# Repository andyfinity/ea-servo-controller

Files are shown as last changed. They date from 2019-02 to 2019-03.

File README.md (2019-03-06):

# ExperimentalAvionics Servo Controller

A simple circuit board with just enough smarts to move a servo motor between two adjustable locations.

## About

This project evolved from the need to replace a mechanical actuator inside the engine cowling of a small, experimental airplane.

Position input can be given by a switch, a potentiometer, or an analog signal. Power input is anything from 6V to 18V. Since a switching regulator is used, a higher voltage implies lower current. Servo output is 5V at up to 2A, where the position signal is a 0.5ms to 2.5ms pulse every 20ms.

For your convenience, pinouts are displayed on the back of the PCB.

[Online BOM with vendor links.](https://octopart.com/bom-tool/hhvvhDB6)

## Contributing

[Atmel Studio 7](https://www.microchip.com/mplab/avr-support/atmel-studio-7) is used to compile the source code. [pyupdi](https://github.com/mraardvark/pyupdi/) is then used to push the .hex file to the ATtiny402.

The serial port can be any 3.3V UART-to-USB device, but we used [this one](https://www.tinyosshop.com/index.php?route=product/product&product_id=600). 5V will probably work, but it's untested.

PRs are welcome. There's not a lot of hand-written source code, so just make your edits look nice. If you make any changes to the PCB or schematic, make sure ERC and DRC come back mostly clean.

## License

Everything is released under the GPLv3.

## TODO

* Release the source code and .hex file
* Show pictures in README
* Design basic enclosure
* Release PCB STEP file
* Think about replacing the ATtiny with a bunch of discrete parts
* Think about increasing the 5V rail to 6V to increase motor speed

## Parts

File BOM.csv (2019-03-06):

Qty | Manufacturer | MPN | Schematic Reference | Digi-Key SKU
1 | Microchip | ATTINY402-SSFR | U1 | ATTINY402-SSFRCT-ND
1 | Texas Instruments | TPS82140SILR | U2 | 296-48215-1-ND
2 | Microchip | MCP1754ST-3302E/CB | U3, U4 | MCP1754ST-3302E/CBCT-ND
1 | ON Semiconductor | BSS138 | Q1 | BSS138CT-ND
1 | Infineon | IRLML9301TRPBF | Q2 | IRLML9301TRPBFCT-ND
2 | Dialight | 598-8220-107F | D1, D2 | 350-2048-1-ND
1 | ON Semiconductor | SZMMSZ4697T1G | D3 | SZMMSZ4697T1GOSCT-ND
1 | Samsung | CL10B104KB8NNNC | C1 | 1276-1000-1-ND
2 | Samsung | CL21A475KAQNNNE | C2, C4 | 1276-1244-1-ND
2 | Samsung | CL21B105KAFNNNE | C3, C5 | 1276-1066-1-ND
2 | Samsung | CL31A106KAHNNNE | C6, C9 | 1276-1075-1-ND
1 | Murata | GRM219R61C226ME15L | C7 | 490-9952-1-ND
1 | Samsung | CL10B103KB8NCNC | C8 | 1276-1921-1-ND
2 | BI Technologies | 23BR500LFTR | R1, R2 | 987-1805-1-ND
1 | Panasonic | ERJ-3GEYJ472V | R5 | P4.7KGCT-ND
3 | Panasonic | ERJ-3GEYJ102V | R6, R7, R15 | P1.0KGCT-ND
5 | Panasonic | ERJ-3GEYJ101V | R4, R8, R9, R10, R13 | P100GCT-ND
2 | Panasonic | ERJ-3GEY0R00V | R3, R16 | P0.0GCT-ND
1 | Panasonic | ERJ-3EKF5233V | R11 | P523KHCT-ND
1 | Panasonic | ERJ-3EKF1003V | R12 | P100KHCT-ND
1 | FCI | LD09P24A4GV00LF | P1 | 609-5184-ND
1 | ON Semiconductor | MBR130LSFT1G | D4 | MBR130LSFT1GOSCT-ND

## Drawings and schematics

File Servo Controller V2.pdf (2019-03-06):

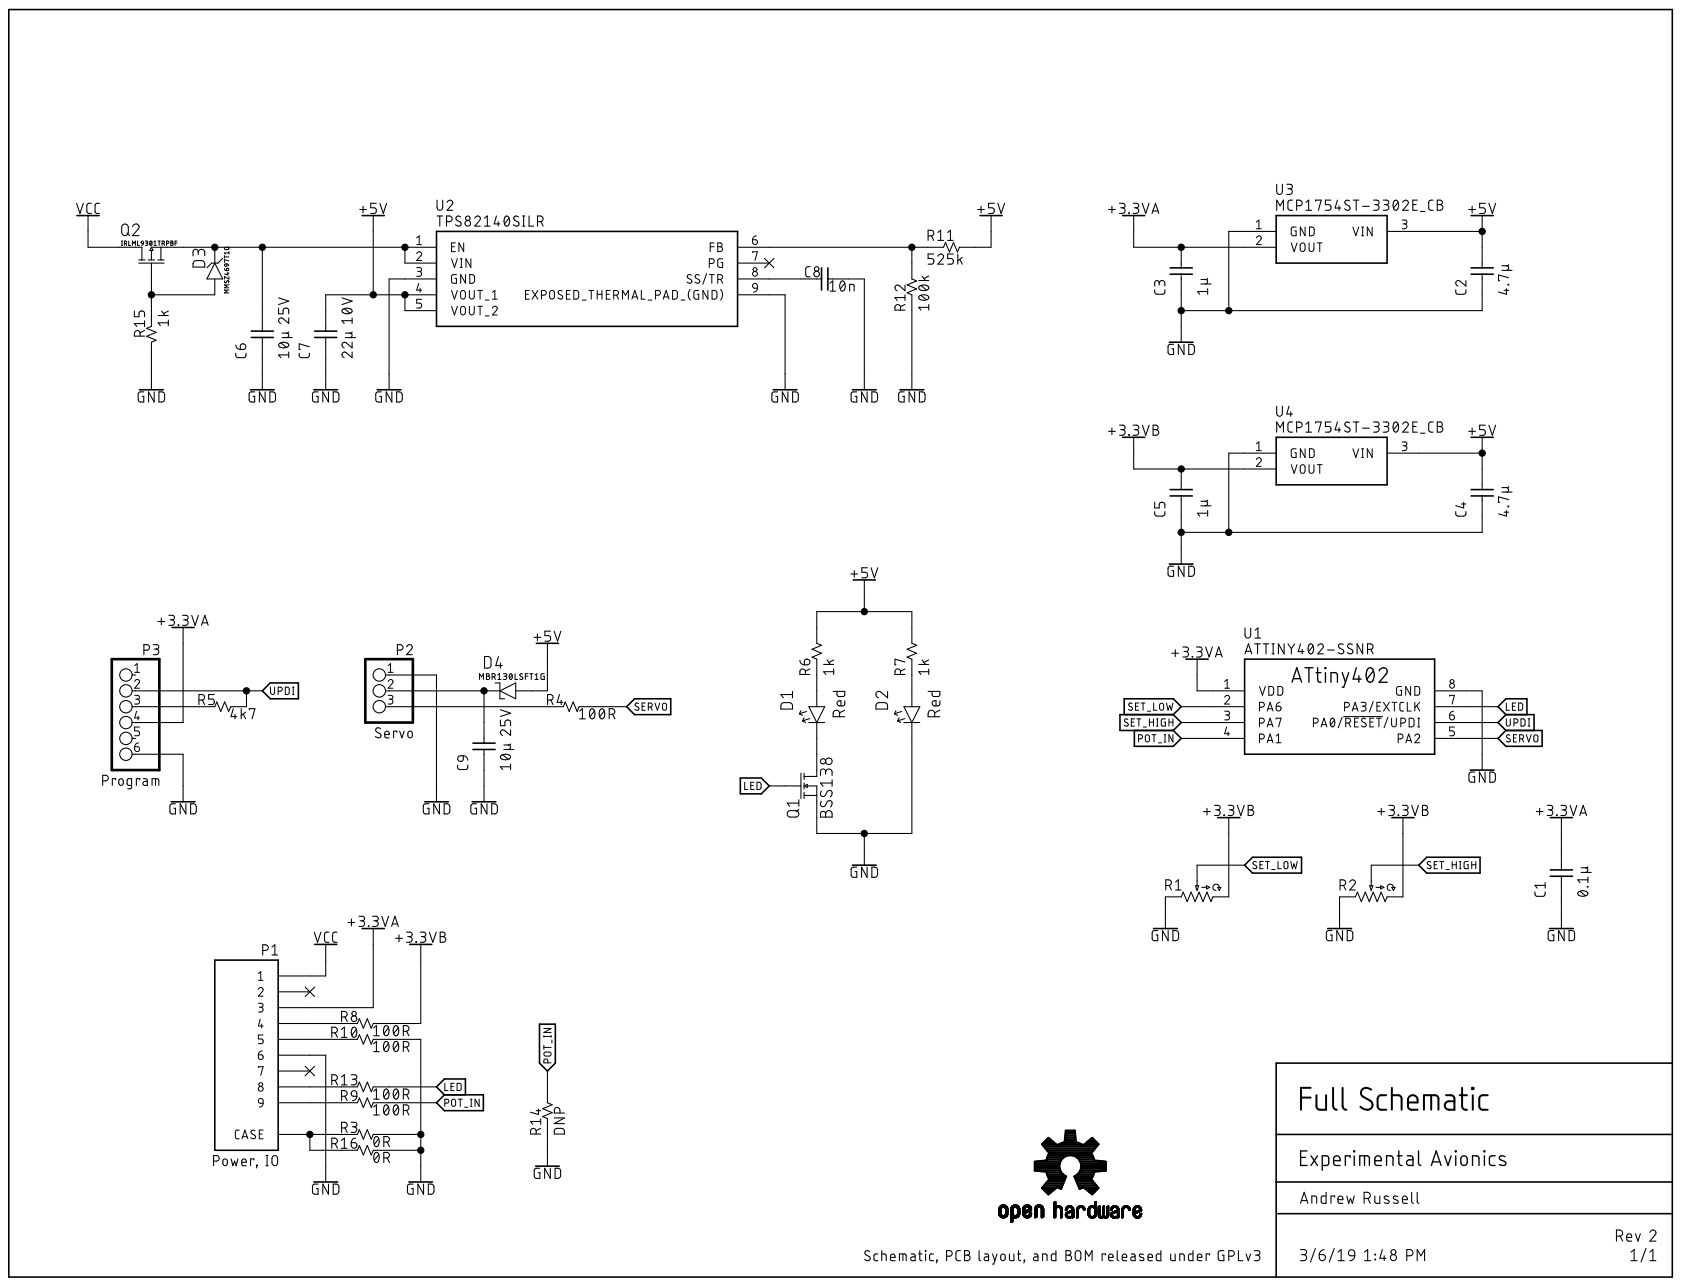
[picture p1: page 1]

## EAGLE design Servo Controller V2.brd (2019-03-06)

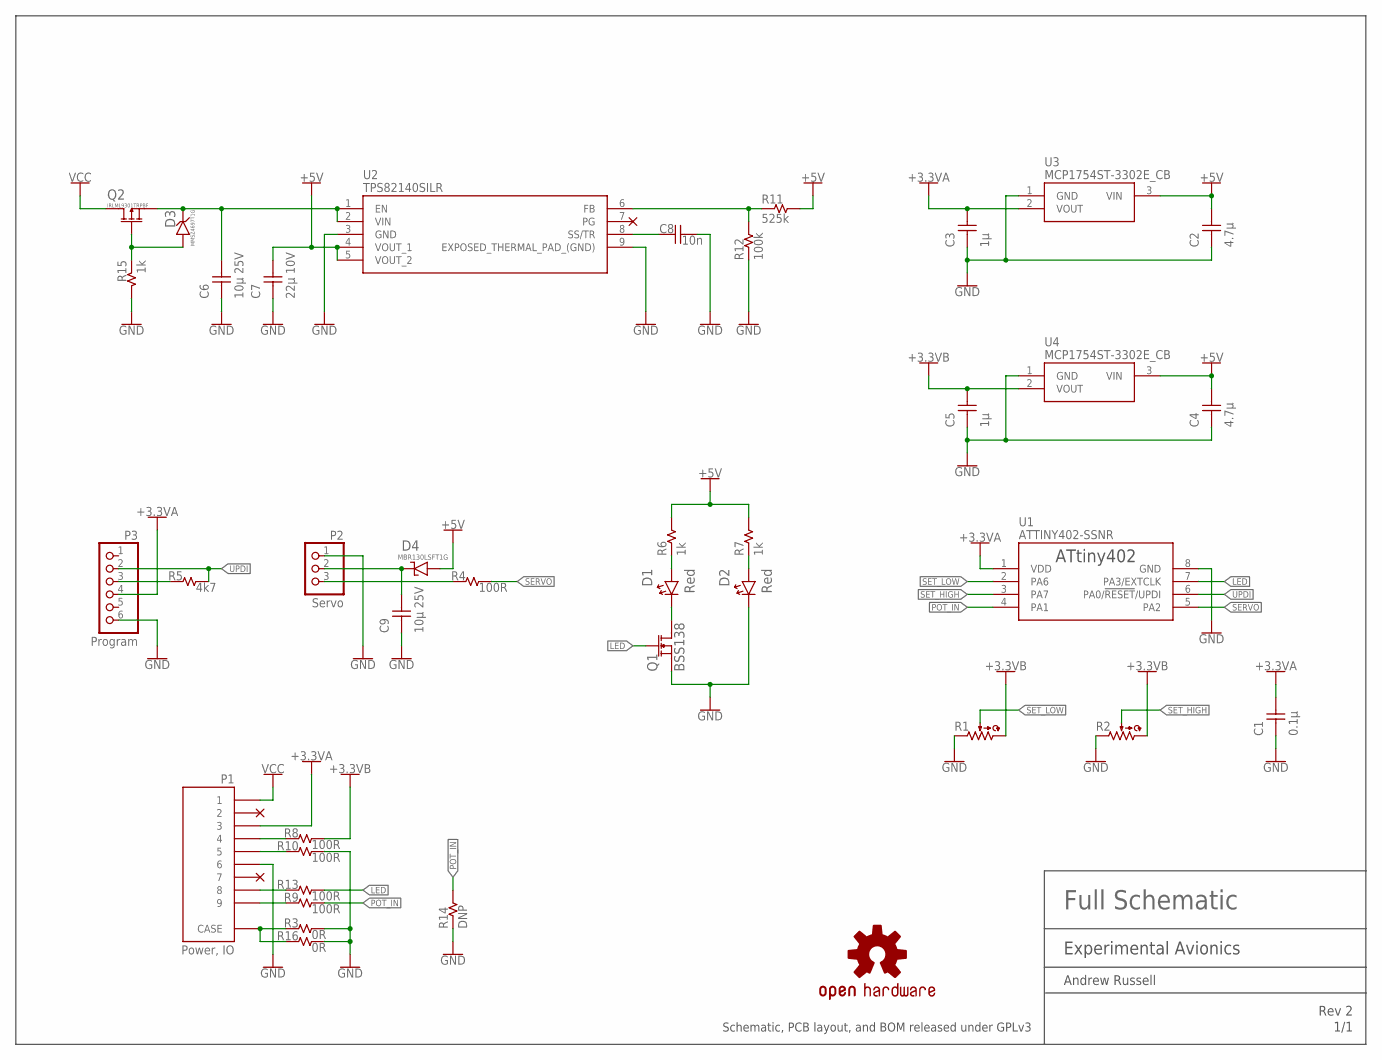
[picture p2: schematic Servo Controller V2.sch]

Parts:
C1: 0.1µ; CAPC1608X90
C2, C4: 4.7µ; CAPC2012X90
C3, C5: 1µ; CAPC2012X90
C6, C9: 10µ 25V; CAPC3216X180
C7: 22µ 10V; CAPC2012X90
C8: 10n; CAPC1608X90
D1, D2: Red; SODFL3216X68
D3: MMSZ4697T1G; SODFL3518X115
D4: MBR130LSFT1G; SODFL3616X98
LOGO1: OSHW-LOGOMINI; OSHW-LOGO-MINI
P1: Power, IO; D09P24A4GV00LF
P2: Servo; 1X03/90
P3: Program; 1X06
Q1: BSS138; SOT95P240X110-3
Q2: IRLML9301TRPBF; SOT95P240X110-3
R1, R2: POTENTIOMETER; TT_23B
R3, R16: 0R; RESC1608X55
R4, R8, R9, R10, R13: 100R; RESC1608X55
R5: 4k7; RESC1608X55
R6, R7, R15: 1k; RESC1608X55
R11: 525k; RESC1608X55
R12: 100k; RESC1608X55
R14: DNP; RESC1608X55
U1: ATTINY402-SSNR; SOIC127P599X175-8
U2: TPS82140SILR; SIL0008D
U3, U4: MCP1754ST-3302E_CB; SOT95P255X145-3N

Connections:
+3V3A: C1.2, C3.2, P1.P$3 (3), P3.4, U1.1 (VDD), U3.2 (VOUT)
+3V3B: C5.2, R1.P$3, R2.P$3, R8.2, U4.2 (VOUT)
+5V: C2.2, C4.2, C7.2, D4.2 (A), R6.2, R7.2, R11.2, U2.4 (VOUT_1), U2.5 (VOUT_2), U3.3 (VIN), U4.3 (VIN)
GND: C1.1, C2.1, C3.1, C4.1, C5.1, C6.1, C7.1, C8.2, C9.1, D2.1 (C), P1.P$6 (6), P2.1, P3.6, Q1.2 (S), R1.P$1, R2.P$1, R3.2, R10.2, R12.1, R14.1, R15.2, R16.2, U1.8 (GND), U2.3 (GND), U2.9 (EXPOSED_THERMAL_PAD_(GND)), U3.1 (GND), U4.1 (GND)
LED: Q1.1 (G), R13.2, U1.7 (PA3/EXTCLK)
unnamed: P3.3, R5.1
unnamed: C8.1, U2.8 (SS/TR)
unnamed: P1.P$10 (CASE), P1.P$11 (CASE), R3.1, R16.1
unnamed: D1.2 (A), R6.1
unnamed: R11.1, R12.2, U2.6 (FB)
unnamed: P1.P$9 (9), R9.1
unnamed: P1.P$5 (5), R10.1
unnamed: D2.2 (A), R7.1
unnamed: D1.1 (C), Q1.3 (D)
unnamed: P2.3, R4.1
unnamed: P1.P$4 (4), R8.1
unnamed: P1.P$8 (8), R13.1
unnamed: D3.2 (A), Q2.1 (G), R15.1
unnamed: C6.2, D3.1 (C), Q2.2 (S), U2.1 (EN), U2.2 (VIN)
unnamed: C9.2, D4.1 (C), P2.2
POT_IN: R9.2, R14.2, U1.4 (PA1)
SERVO: R4.2, U1.5 (PA2)
SET_HIGH: R2.P$2, U1.3 (PA7)
SET_LOW: R1.P$2, U1.2 (PA6)
UPDI: P3.2, R5.2, U1.6 (PA0/!RESET!/UPDI)
VCC: P1.P$1 (1), Q2.3 (D)

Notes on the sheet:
Schematic, PCB layout, and BOM released under GPLv3

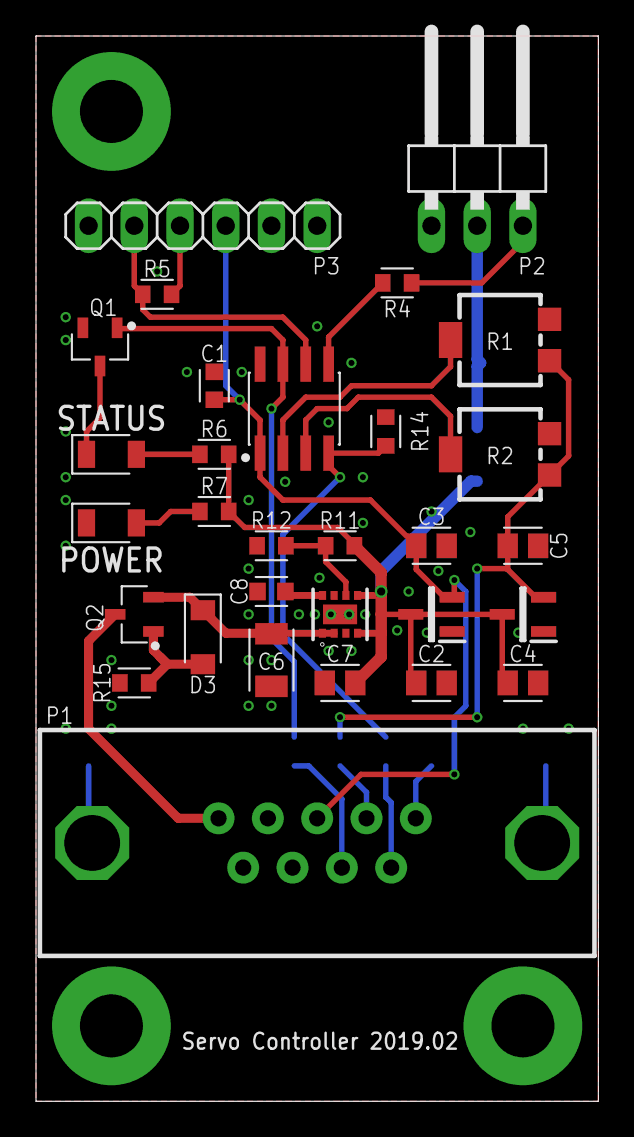
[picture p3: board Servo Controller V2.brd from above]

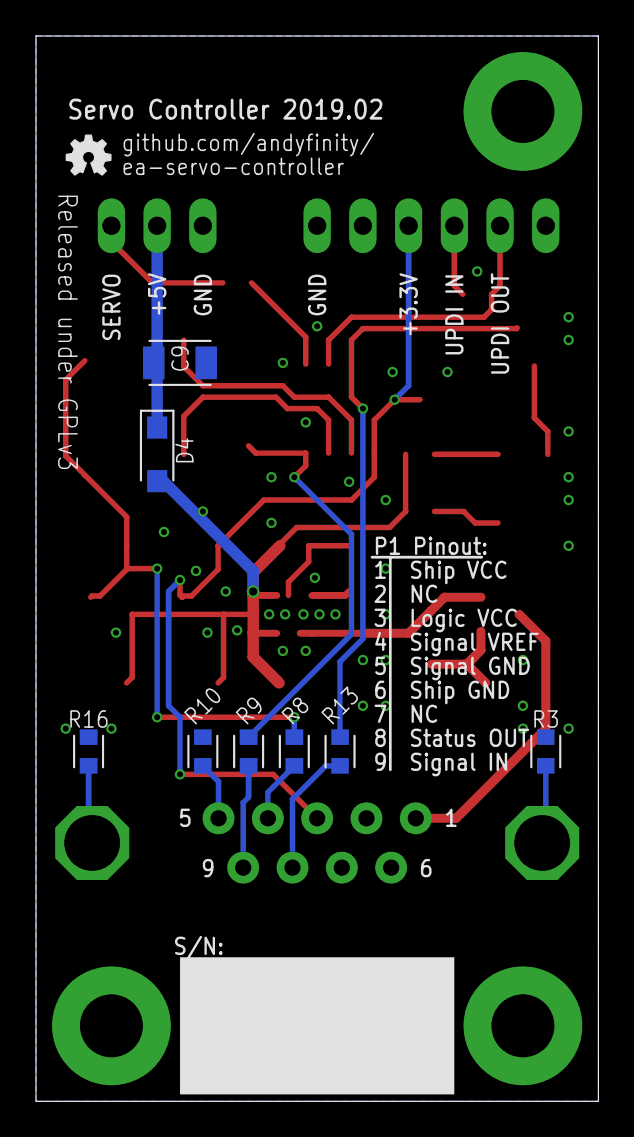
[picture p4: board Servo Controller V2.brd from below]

Board: 2 copper layers, 31.2 x 59.2 mm, 39 parts (9 on the bottom side), 26 nets.

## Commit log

2019-02-25 Initial release
    [BOM.csv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]
2019-03-06 Eliminated back EMI on the 5V rail from a large motor braking.
    [BOM.csv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]
2019-03-06 Display OSHW logo on schematic.
    [Servo Controller V2.brd, Servo Controller V2.sch]

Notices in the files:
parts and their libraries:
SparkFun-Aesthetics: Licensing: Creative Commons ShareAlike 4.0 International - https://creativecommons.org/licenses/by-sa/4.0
